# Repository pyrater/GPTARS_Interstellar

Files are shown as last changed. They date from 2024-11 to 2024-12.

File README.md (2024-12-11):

My Modifications and documentation of the build.
All files printed on Bambu Labs P1S
All "Flexor" parts to be printed in TPU, all others PETG

TPU: https://us.store.bambulab.com/products/tpu-for-ams

PETG: https://us.store.bambulab.com/products/petg-hf

The Default v9 chasis bottom does not allow for installation of a SD card, too close to the wall. Modified that part... will test.  (Chassis Bottom (Mod SD CARD).stl)

Plan:
LLM = ooba/openai/tabby (recommend https://github.com/theroyallab/tabbyAPI)
TTS = local or xttsv2 using xtts-api-server WITH VOICE clone (https://github.com/daswer123/xtts-api-server)
STT = uses vosk
SD = Automatic1111
Vision = Image Classifier

Good Info: https://www.instagram.com/wizard.py/

wizard uses the MG996R 55g Digital RC Servo Motors High Torque Metal Gear Servo
Andrew uses: diymore 6PCS Metal Gear High Speed Torque Digital Servo Moto

-Link: https://www.amazon.com/diymore-6-Pack-MG996R-Digital-Helicopter/dp/B0CGRP59HJ/ref=sr_1_5?sr=8-5

Printing Draft / test is complete:
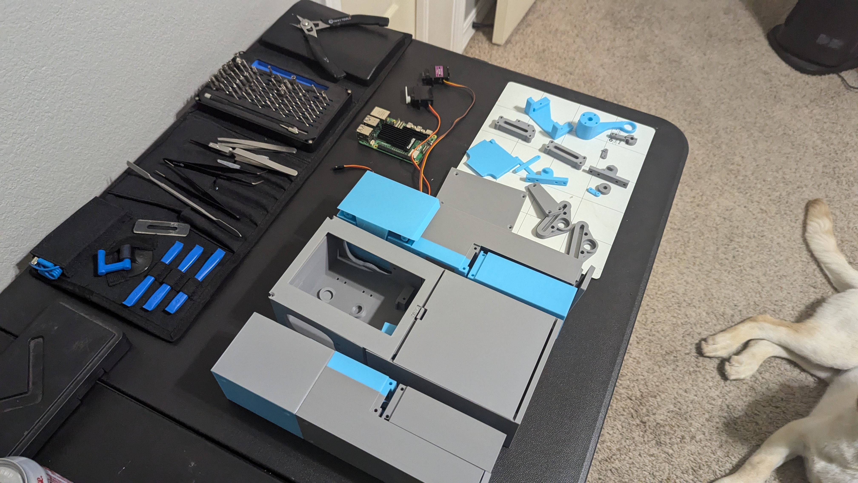
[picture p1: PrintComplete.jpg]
print


Software Demo (all locally hosted RTX 3060 streaming to RPI):
Video Title (https://www.youtube.com/watch?v=4YObs8BV3Mc)

My Hardware:

Screws Needed (atleast):

6  M3 20mm

40 M3 14mm

76 M3 10mm

Rods:
https://www.amazon.com/gp/product/B01MAYQ12S/ref=ox_sc_act_title_1?smid=ATVPDKIKX0DER&psc=1
https://www.amazon.com/gp/product/B0CTSX8SJS/ref=ox_sc_act_title_2?smid=A1NR50YASSZD11

Servos:
https://www.amazon.com/gp/product/B0CGRP59HJ/ref=ox_sc_act_title_3?smid=A3F3CVCOVVNP2J

NOTE: Each leg APPEARS to need 2 90g micro servos if you want exendable arms.

Bolts:
https://www.amazon.com/gp/product/B0CR6DY4SS/ref=ox_sc_act_title_4?smid=A1ZRRCZIF57JQ9
https://www.amazon.com/gp/product/B0D9GW9K4G/ref=ox_sc_act_title_5?smid=A1ZRRCZIF57JQ9
https://www.amazon.com/gp/product/B0CR6G5XWC/ref=ox_sc_act_title_6?smid=A1ZRRCZIF57JQ9
https://www.amazon.com/gp/product/B0CR6F3N45/ref=ox_sc_act_title_7?smid=A1ZRRCZIF57JQ9

Springs:
https://www.amazon.com/gp/product/B076M6SFFP/ref=ox_sc_act_title_8?smid=A1THAZDOWP300U&psc=1

Bearings:
https://www.amazon.com/gp/product/B07FW26HD4/ref=ox_sc_act_title_9?smid=ATVPDKIKX0DER&psc=1

16-Channel 12-bit PWM Servo Driver with I2C Interface:
https://www.amazon.com/gp/product/B00EIB0U7A/ref=ox_sc_act_title_10?smid=AAEX2EKCSXB7D&psc=1

RPI Mic:
https://www.amazon.com/gp/product/B086DRRP79/ref=ox_sc_act_title_11?smid=A1DWLG2LHSJB8R

Linkage:
https://www.amazon.com/gp/product/B0CRDRWYXW/ref=ox_sc_act_title_12?smid=A1NR50YASSZD11&psc=1

Buck Convertor:
https://www.amazon.com/gp/product/B07SGJSLDL/ref=ox_sc_act_title_13?smid=A3CX4TQNUXMB0L

RPI 5:
https://www.amazon.com/Raspberry-Pi-Quad-core-Cortex-A76-Processor/dp/B0CTQ3BQLS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

3" LCD:
https://www.amazon.com/OSOYOO-3-5inch-Display-Protective-Raspberry/dp/B09CD9W6NQ/ref=sr_1_8?sr=8-8

Servo Wires:
https://www.amazon.com/OliYin-7-87in-Quadcopter-Extension-Futaba/dp/B0711TBZY2/ref=sr_1_7?sr=8-7

MISC:

Audio amp:
https://www.amazon.com/dp/B0BTBS5NW2

Audio Speaker:
https://www.amazon.com/dp/B07GJ4GH67

Camera:
https://www.amazon.com/dp/B07GJ4GH67

Orginal Fork info:

# TARS from Interstellar x ChatGPT

- Original article: https://www.hackster.io/charlesdiaz/how-to-build-your-own-replica-of-tars-from-interstellar-224833#comments

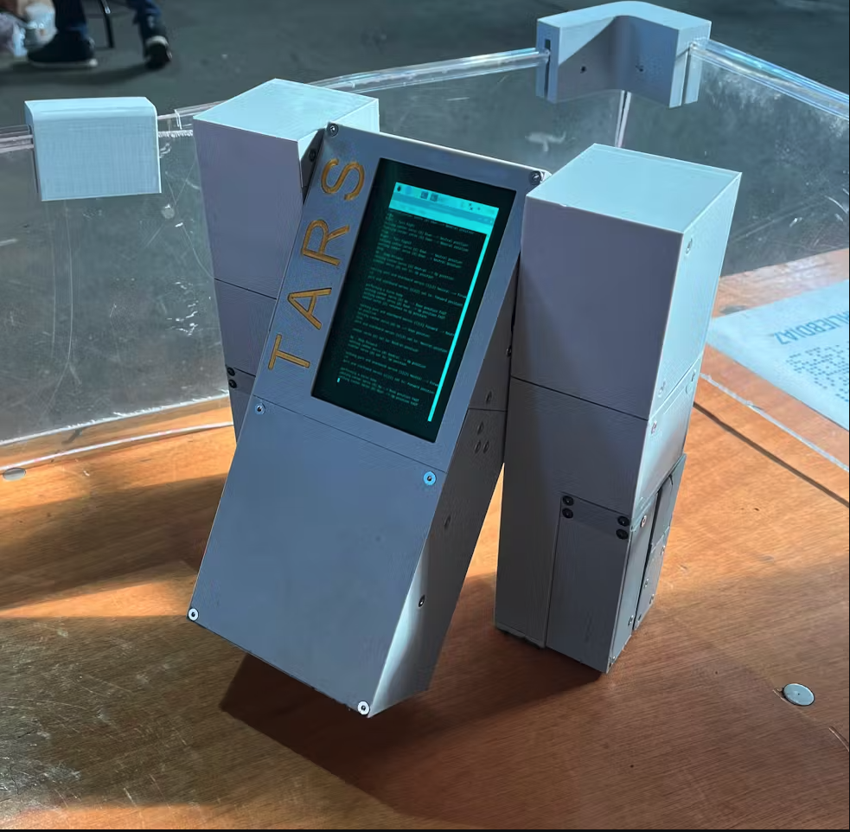
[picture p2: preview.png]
preview


## Files TARS v3_10 - Fix Case Clip

- DOWNLOAD: https://uploadnow.io/f/MPLCGwg | https://fastupload.io/9f3621ef4afe07cc

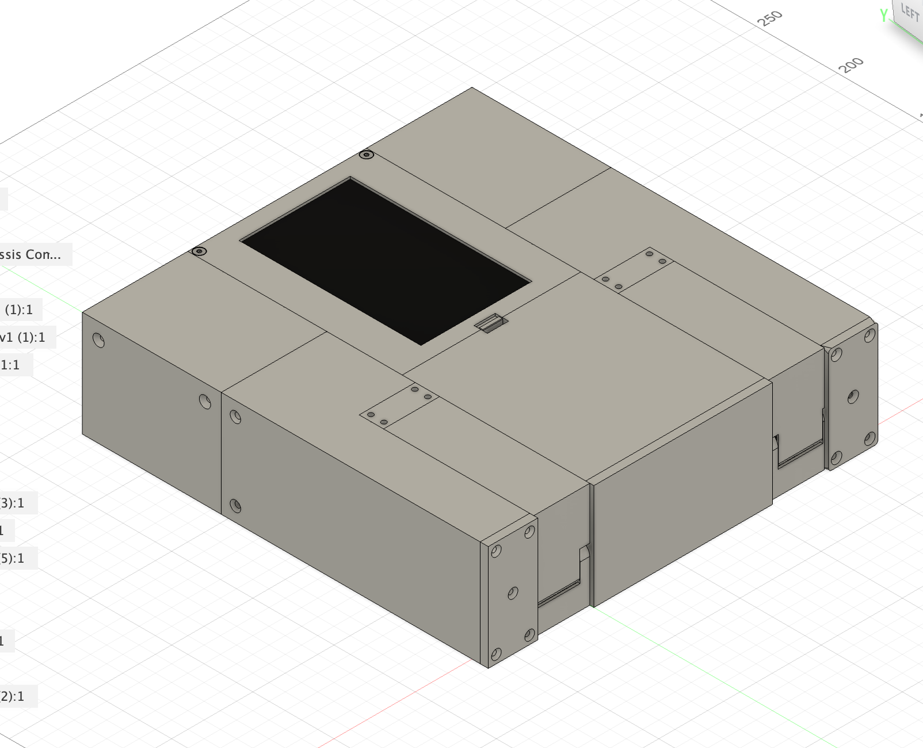
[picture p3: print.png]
print


## Software

- Fusion 360 at https://www.autodesk.com/ca-en/products/fusion-360/personal
- https://projects.raspberrypi.org/en/projects/getting-started-with-the-pico/2
- OS Pi: https://www.raspberrypi.com/software/

## Tutorial

- OS SD Card: https://www.tomshardware.com/how-to/set-up-raspberry-pi

### Adafruit 16-Channel PWM HAT with a Raspberry Pi

- Videos https://www.youtube.com/watch?v=bB-xymRI8BY,
- Documentation: https://learn.adafruit.com/adafruit-16-channel-pwm-servo-hat-for-raspberry-pi, https://core-electronics.com.au/guides/raspberry-pi/servo-hat-raspberry-pi/

### Without HAT

- Videos: https://www.youtube.com/watch?v=ea6tSppgZlY, https://www.youtube.com/watch?v=9jcEwn7GzNs, https://www.youtube.com/watch?v=40tZQPd3z8g
- Documentation: https://learn.adafruit.com/adafruits-raspberry-pi-lesson-8-using-a-servo-motor/overview, https://learn.adafruit.com/adafruit-16-channel-servo-driver-with-raspberry-pi/configuring-your-pi-for-i2c, https://www.youtube.com/watch?v=-x2EEIUMm6A

## 3D Printing

- Steel / Stainless / Aluminium: https://forgelabs.ca/
- PLA / ABS: https://jlc3dp.com/3d-printing-quote or https://www.treatstock.com/

## Hardware

#### Power

- 1 x 12V to 6V 3A DC at https://www.aliexpress.com/item/32968137531.html
- https://www.aliexpress.com/item/1005003160082010.html
- 1 x 5V DC 4A Fixed 2.1mm Tip Appliance Plugpack at https://www.amazon.ca/Power-Adapter-100-240V-Transformers-Supply/dp/B087LY41PV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
- 1 x 5V 4A DC Power Adapter at https://www.aliexpress.com/item/1005004589869667.html (Used for testing before buying battery)
- 1 x 5V USB To DC DC Power Cable 5.5\*2.1m at https://www.aliexpress.com/item/1005007296667037.html
- 200000mAh Portable Solar Power Bank External Battery Fast Charging Waterproof Powerbank with SOS Flashlight Poverbank for Xiaomi at https://www.aliexpress.com/item/1005006959367711.html, https://www.aliexpress.com/item/1005007306992861.html

Please use HDMI cable: fpv cable hdmi, HDMI-compatible,FPV HDMI ffc HDMI Ribbon Cable 90 Degree Mini/Micro HDMI to Standard HDMI PCB Connector 20pin fpv micro hdmi 15cm

---

#### Hardware

- 1 x https://www.aliexpress.com/item/32914198349.html

- 2 x Lightweight Actobotics Servo Horn (H25T Spline) at https://www.servocity.com/25t-lightweight-hub-horn/ or look at .step file
- 1 x Adafruit 16-Channel 12-bit PWM/Servo Driver at https://www.adafruit.com/product/2327
- 1 x 8Bitdo Zero 2 Bluetooth at https://www.aliexpress.com/item/1005006458561670.html
-
- 5 x LD-3015MG 17KG 270 (LewanSoul LD-3015MG Standard Full Metal Gear Digital Servo with 17kg High Torque Dual Ball Bearing for RC Robot Car) at https://www.aliexpress.com/item/32787763122.html (2000-0025-0002)
- 1 x Fataba s3003 90-180deg at https://www.aliexpress.com/item/32957714272.html
- 4 x 2903-0004-0245 assembly at https://www.gobilda.com/2903-series-nylon-ball-linkage-m4-24-5mm-length-4-pack / Linkeage Rod M4 at https://www.aliexpress.com/item/1005005616106307.html
- 10 x Flexor bolts at https://www.aliexpress.com/item/32969042589.html

- 10 x Hex M3 20mm, 10 x Hex M3 10mm, 10 x Hex M3 14mm, 10 x Hex M3 30mm at https://www.aliexpress.com/item/1005003184392748.html
- 1 x Bearing 6x15x5 https://www.aliexpress.com/item/4000909583668.html
- 1 x Compression Spring 0.5mmx20mmx11mm https://www.aliexpress.com/item/1005005312536098.html

---

#### CPU & Storage

- 1 x MicroSD Card at https://www.aliexpress.com/item/1005006693506827.html
- 1 x Raspberri 3B/3B+ at https://www.adafruit.com/raspberrypi3bplus or eBay
- 1 x Elecrow 5 inch Touchscreen Portable Monitor HDMI-compatible 800x480 at https://www.aliexpress.com/item/32889893278.html

---

#### Battery

- 1 x myCharge Hub Mini at https://www.target.com/p/mycharge-hub-mini-3350mah-2-4a-output-power-bank-with-integrated-charging-cables-silver/-/A-76625534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
- 1 x Zeee 11.1V 120C 1500mAh 3S at https://www.amazon.ca/Zeee-Graphene-Quadcopter-Airplane-Helicopter/dp/B08P399N54/

## Extra

- Face Recognition: https://core-electronics.com.au/guides/face-identify-raspberry-pi/
- Lidar Detection: MS200 Lidar Sensor Kit Portable 360°TOF Ranging Scanner 12m Range Support ROS1 and ROS2 For ROS Robot Raspberry Pi Jetson NANO
- Battery Level: https://learn.sparkfun.com/tutorials/ltc4150-coulomb-counter-hookup-guide, https://forums.raspberrypi.com/viewtopic.php?t=173046, https://forums.raspberrypi.com/viewtopic.php?t=340930

## ChatGPT

- https://www.youtube.com/watch?v=N0718RfpuWE

## Servo Abstractor - Python

> Sort of redundant to give these functions their own file, but this program takes the basic servo movements from the servo controller file and combines them to automate walking functions.

## TARS Runner - Python

> Run this file in terminal on your onboard computer to initialize TARS. This file handles communication with the bluetooth remote.

## Servo Controller - Python

> Handles basic movements of servos in TARS. Communicates with an Adafruit PCA9685 servo driver to control the servos.

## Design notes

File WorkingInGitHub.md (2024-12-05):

# Contributing to GPTARS_Interstellar

Welcome to the GPTARS_Interstellar community! We're excited to have you contribute code, CAD files, documentation, or related content to this project. This guide is for folks new to GitHub to help you quickly get setup to collaborate on the project.

> "Everybody good? Plenty of slaves for my robot colony?" -TARS

---

## **What You Can Contribute**
This project includes:
- **Binary CAD files** (e.g., STEP, STL)
- **Code**
- **Documentation**
- **Related content**

The primary repository is maintained by pyrater: [GPTARS_Interstellar on GitHub](https://github.com/pyrater/GPTARS_Interstellar).
Join us in discord https://discord.gg/UfQpGXPW #repo for related questions and discussions.
---

## **For Experienced GitHub Users**
- Fork the repo and submit pull requests (PRs) to [pyrater/GPTARS_Interstellar](https://github.com/pyrater/GPTARS_Interstellar).
- Notify pyrater on Discord in the `#repo` channel if your PR is ready for review.

---

## **For New Git and GitHub Users**

Never used Git or GitHub before? No problem! This section will guide you through the basic steps to get started.

### **Step 1: Create a GitHub Account**
- Sign up for a free GitHub account: [Create an account](https://docs.github.com/en/get-started/start-your-journey/creating-an-account-on-github).

### **Step 2: Fork the Repository**
1. Go to [GPTARS_Interstellar on GitHub](https://github.com/pyrater/GPTARS_Interstellar).
2. Click the **Fork** button in the top-right corner.
3. Select **Create a new fork** to make your own copy of the repository. This fork will look like `yourGithubUsername/GPTARS_Interstellar`.

Why fork? Forking allows you to make changes in your own copy of the repository without affecting the original.

### **Step 3: Install Git Locally**
If you’re new to Git, you’ll need to install it on your local machine.
- Download Git: [Git Downloads](https://git-scm.com/downloads).
- Verify the installation by running `git --version` in your command line.

### **Step 4: Secure Your GitHub Account**
- Protect your account with multi-factor authentication (MFA): [Set up MFA](https://docs.github.com/en/authentication/keeping-your-account-and-data-secure/about-authentication-to-github).
- **Highly Recommended**: Set up an SSH key for secure and streamlined operations: [Generate an SSH Key](https://docs.github.com/en/authentication/connecting-to-github-with-ssh/generating-a-new-ssh-key-and-adding-it-to-the-ssh-agent).

### **Step 5: Clone Your Fork**
1. Open a terminal or command prompt.
2. Navigate to the folder where you want to store the repository.
3. Clone your fork:
   ```bash
   git clone git@github.com:yourGithubUsername/GPTARS_Interstellar.git
   ```
4. Navigate into the project folder:
   ```bash
   cd GPTARS_Interstellar
   ```

### **Step 6: Set Up Remotes**
- Check the remote URLs:
  ```bash
  git remote -v
  ```
  You should see your fork as `origin`.
- Add pyrater's repository as the upstream remote:
  ```bash
  git remote add upstream git@github.com:pyrater/GPTARS_Interstellar.git
  ```

Why? This setup helps you fetch updates from the main repository to keep your fork up-to-date.

---

## **Basic Git Operations**
These are the standard steps for making contributions:

### **1. Create a Branch**
Always create a new branch for your work:
```bash
git checkout -b your-branch-name
```

Branches help you isolate changes and organize features.

### **2. Make Changes**
- Add, edit, or delete files in the project.
- Use descriptive branch names, e.g., `add-new-feature` or `fix-bug`.

### **3. Stage Changes**
Stage your changes to prepare them for a commit:
```bash
git add .
```
Optionally, check the status:
```bash
git status
```

### **4. Commit Changes**
Save your changes locally with a meaningful commit message:
```bash
git commit -m "Your commit message here"
```

For non-binary files, Git tracks changes for version control. For CAD files like STL or STEP, Git stores the files as blobs without versioning.

### **5. Push Changes**
Push your branch to your fork on GitHub:
```bash
git push origin your-branch-name
```

---

## **Creating a Pull Request (PR)**
Once your changes are ready:
1. Go to pyrater's repository: [GPTARS_Interstellar](https://github.com/pyrater/GPTARS_Interstellar).
2. Click **Pull requests** in the top menu.
3. Click the green **New pull request** button.

On the **Comparing changes** page:
- **Base repository**: `pyrater/GPTARS_Interstellar`, base: `main`.
- **Head repository**: `yourGithubUsername/GPTARS_Interstellar`, compare: `your-branch-name`.

### **Provide Details**
- Add a meaningful title for your PR.
- Write a clear description of your changes, explaining what they do and why they’re needed.
- Confirm the changed files are correct.

### **Submit the PR**
- Click **Create pull request**.
- Notify pyrater on Discord in the `#repo` channel.

### **Review and Approval**
- Wait for pyrater to review your PR.
- If changes are requested, update your branch locally, commit, and push again. GitHub will automatically update the PR.
- Once approved, your changes will be merged into the main repository. Congratulations!

---

## **Keeping Your Fork Up-to-Date**
If other contributors make changes to the main repository, keep your fork in sync:
1. Fetch updates from the upstream repository:
   ```bash
   git fetch upstream
   ```
2. Merge updates into your branch:
   ```bash
   git merge upstream/main
   ```
3. Push updates to your fork:
   ```bash
   git push origin your-branch-name
   ```

---

## **Additional Resources**
- [Git Basics](https://git-scm.com/doc)
- [GitHub Docs](https://docs.github.com)
- [Common Git Commands Cheat Sheet](https://education.github.com/git-cheat-sheet-education.pdf)
- [Visual Studio Code - Working with GitHub](https://code.visualstudio.com/docs/sourcecontrol/github)

---

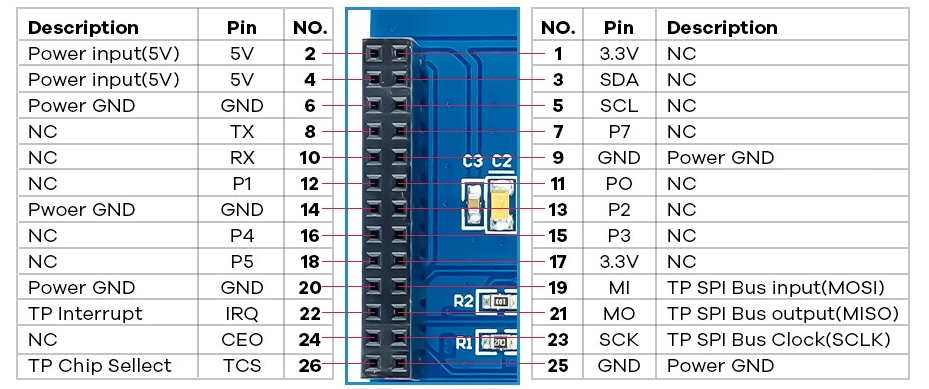
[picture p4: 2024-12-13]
Hardware/Screenshot 2024-12-10 121338.png

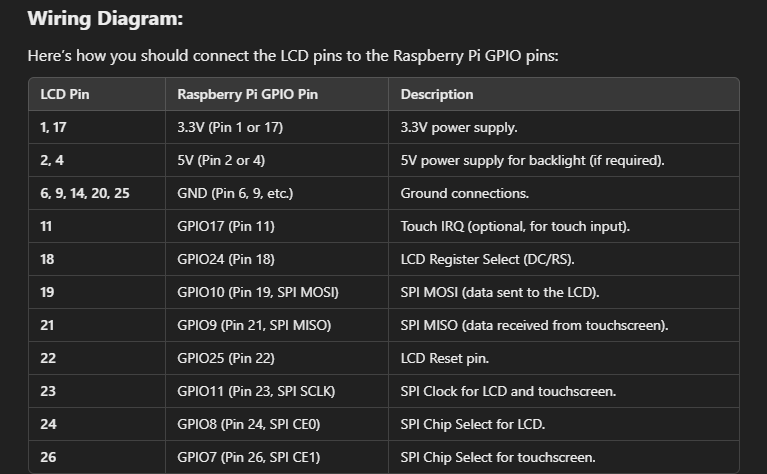
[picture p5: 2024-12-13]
Hardware/Screenshot 2024-12-10 131234.png

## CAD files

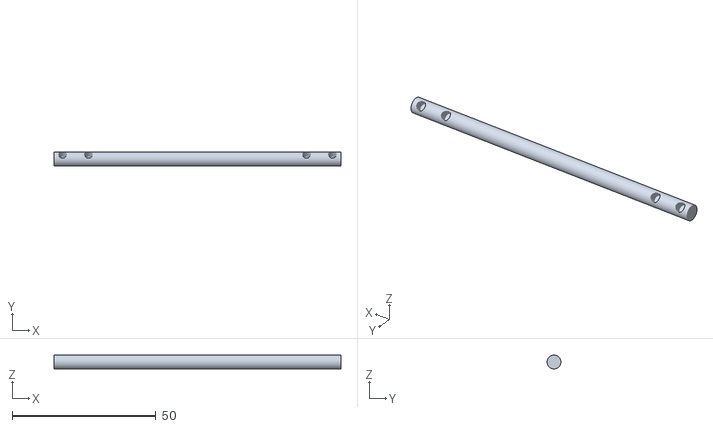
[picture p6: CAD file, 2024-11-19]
3d Printer Files/Main Axle.stl
100.0 x 4.80 x 4.80

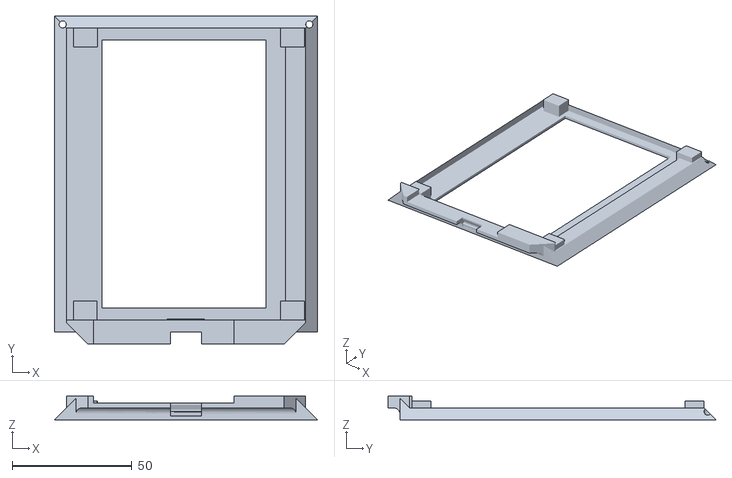
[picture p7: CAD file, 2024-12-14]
3d Printer Files/Chassis Upper Lid MOD 5inch HDMI screen (v10).stl
110.0 x 137.0 x 10.0

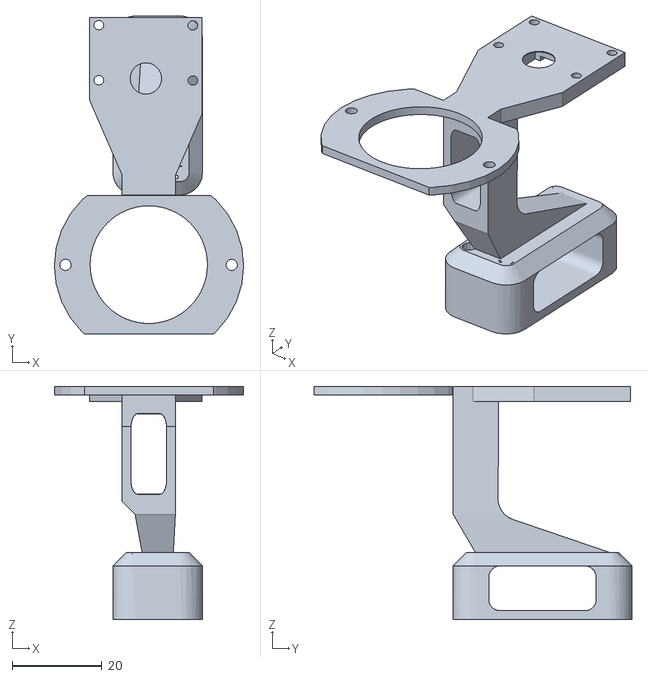
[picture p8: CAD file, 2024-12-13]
3d Printer Files/Other/RPI CAM and Speaker Mount.stl
42.3 x 71.1 x 52.1

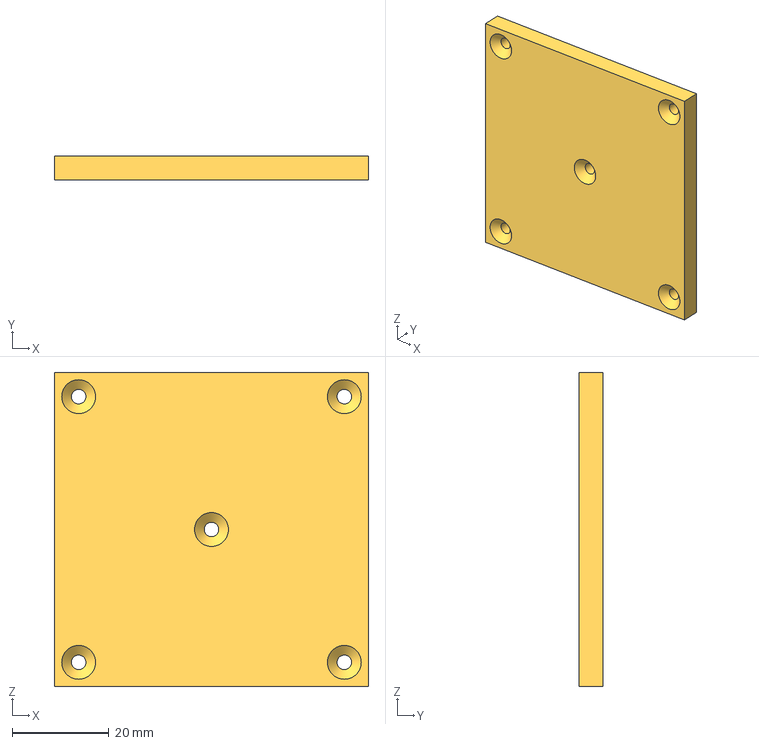
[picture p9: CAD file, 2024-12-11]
3d Printer Files/simplified_tars/footpad-simplified.3mf
65.0 x 5.00 x 65.0 mm

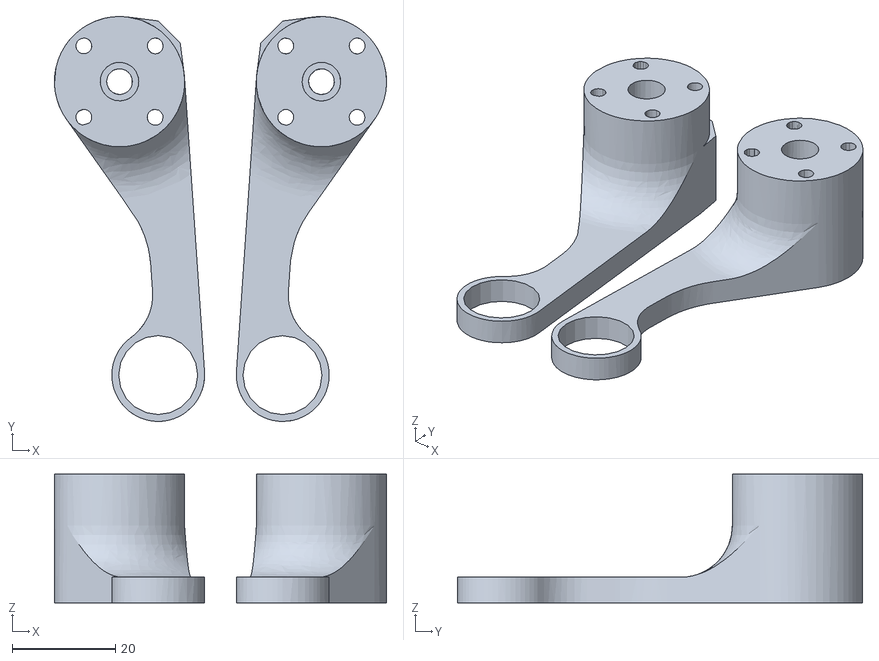
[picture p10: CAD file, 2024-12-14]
3d Printer Files/Arm Right&Left Mount Bigger bearinghole.stl
64.4 x 78.5 x 25.0

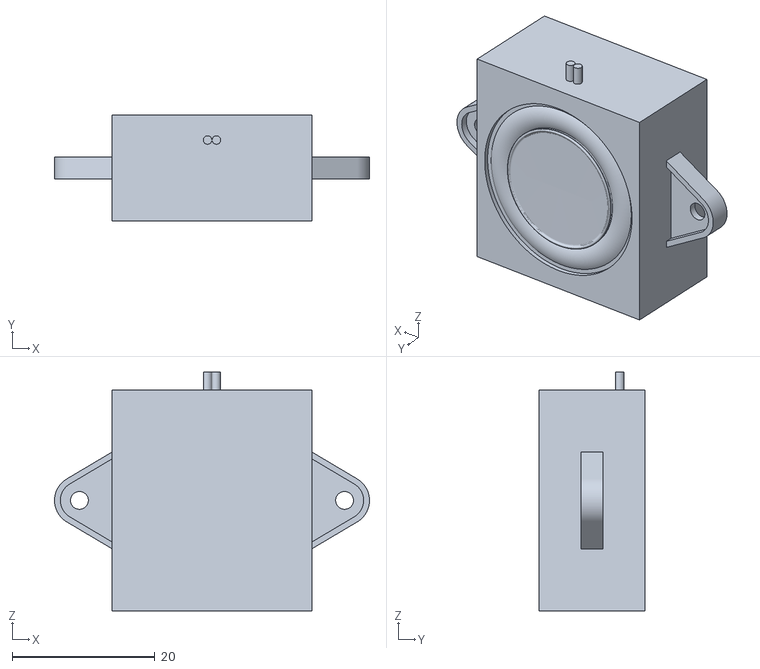
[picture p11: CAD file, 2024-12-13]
3d Printer Files/Other/Speaker.stl
44.2 x 14.9 x 33.5

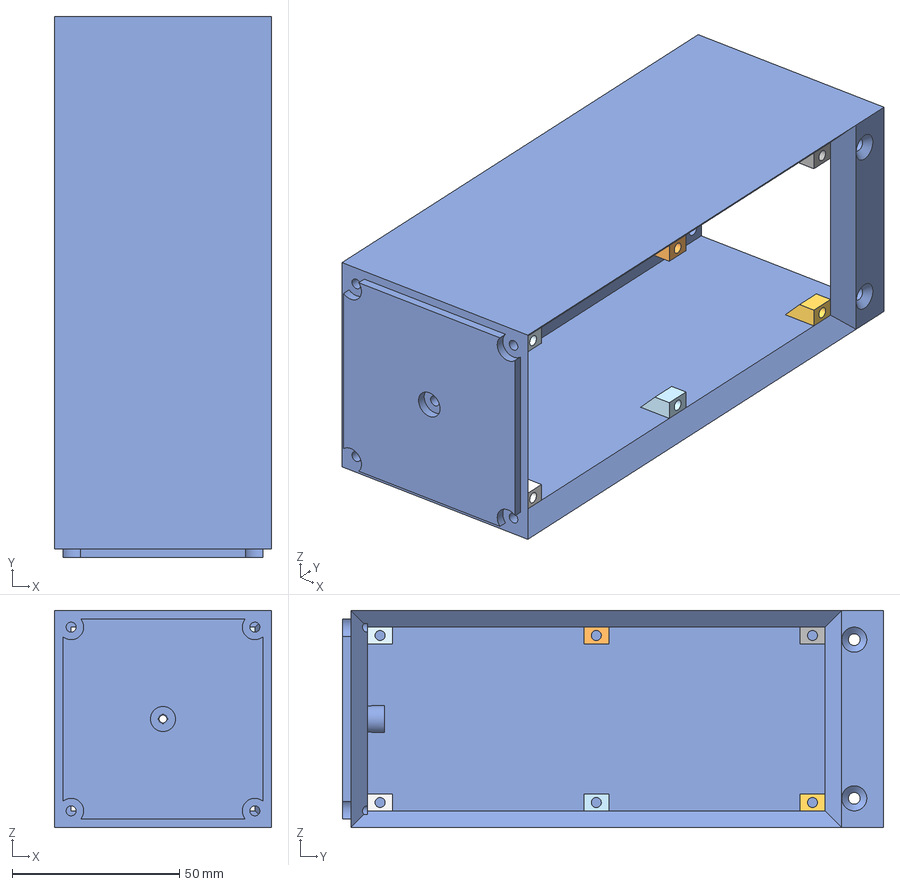
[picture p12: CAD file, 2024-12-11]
3d Printer Files/simplified_tars/leg - simplified.3mf
65.0 x 162.0 x 65.0 mm

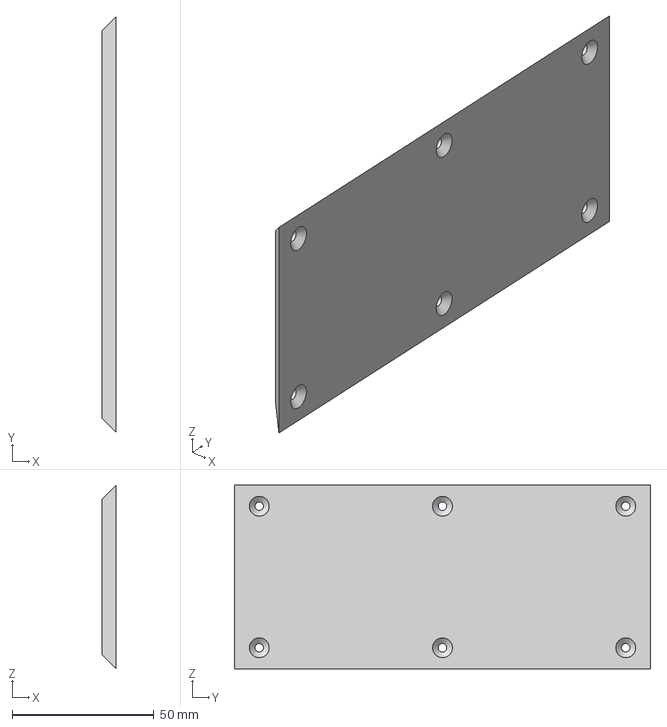
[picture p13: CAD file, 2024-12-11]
3d Printer Files/simplified_tars/leg_simplified-lid.3mf
5.00 x 147.0 x 65.0 mm

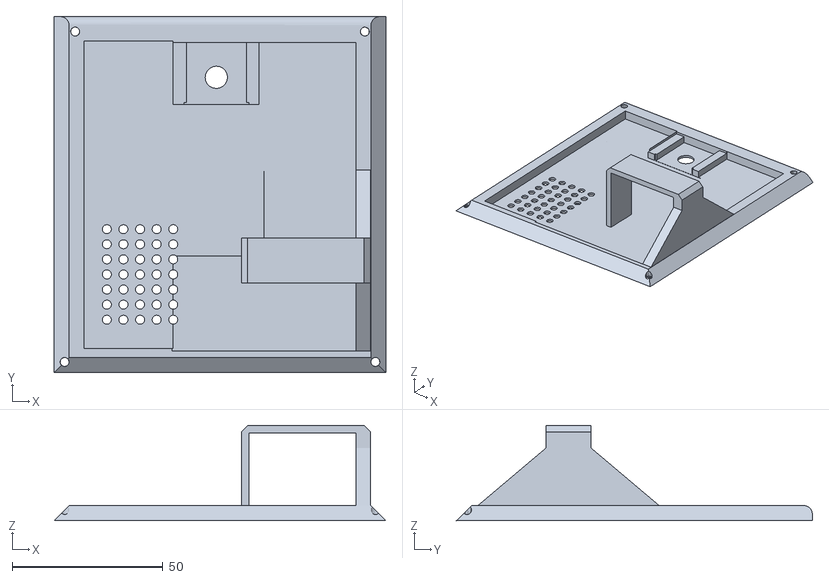
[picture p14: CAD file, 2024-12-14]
3d Printer Files/Chassis Lower Lid MOD LiPo flat-camerahole-speakerholes (v9).stl
110.0 x 118.0 x 31.5

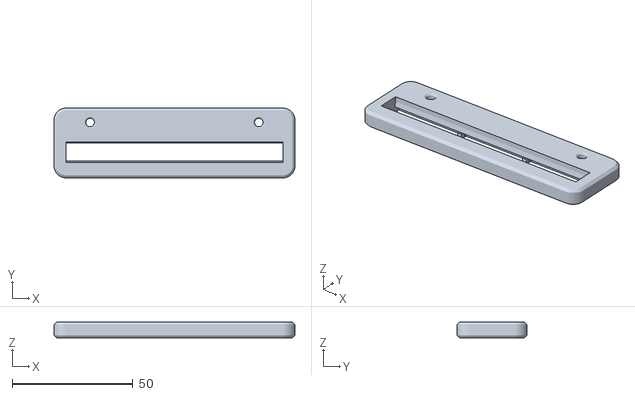
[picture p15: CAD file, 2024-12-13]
3d Printer Files/Other/PCT Linear Base Mount.stl
100.0 x 29.0 x 6.50

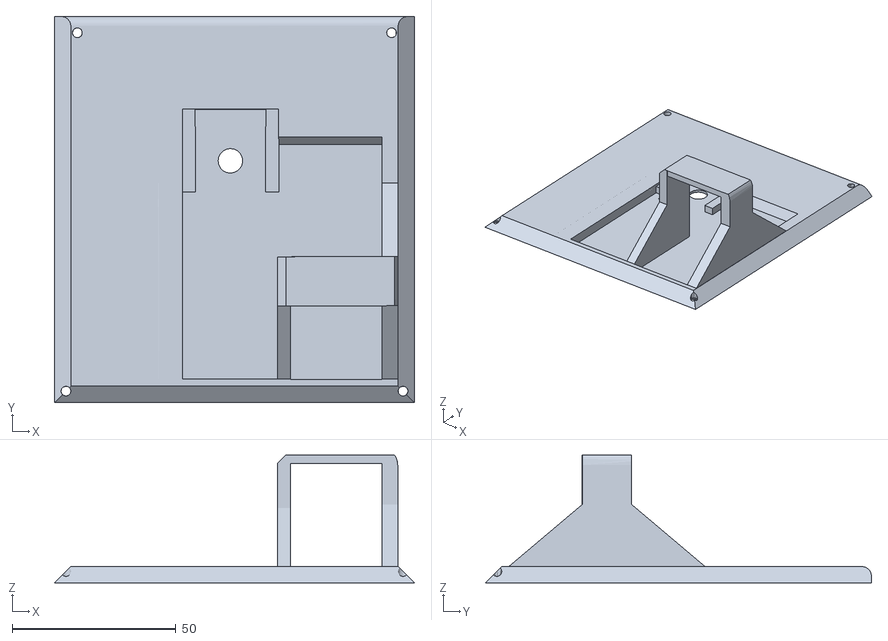
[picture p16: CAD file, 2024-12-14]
3d Printer Files/Chassis Lower Lid MOD LiPo and camerahole- (v9).stl
110.0 x 118.0 x 39.1

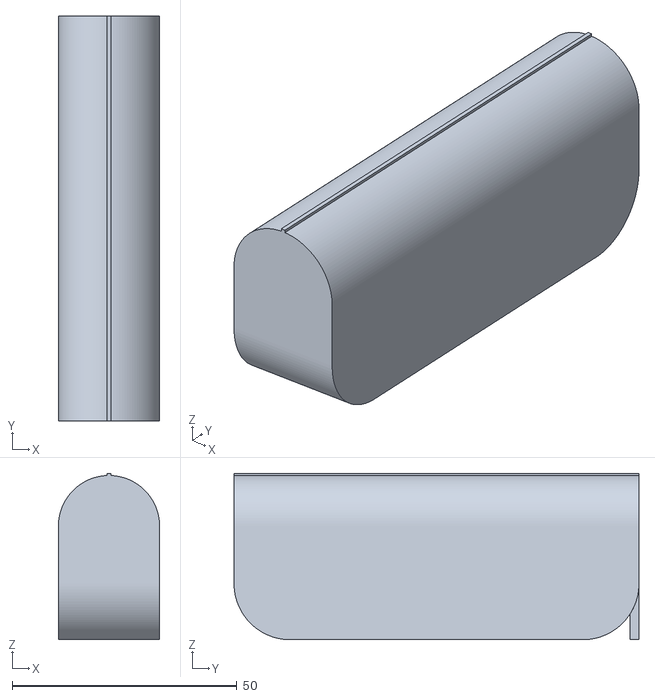
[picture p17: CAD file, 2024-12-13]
3d Printer Files/Other/battery.stl
22.5 x 90.0 x 37.0

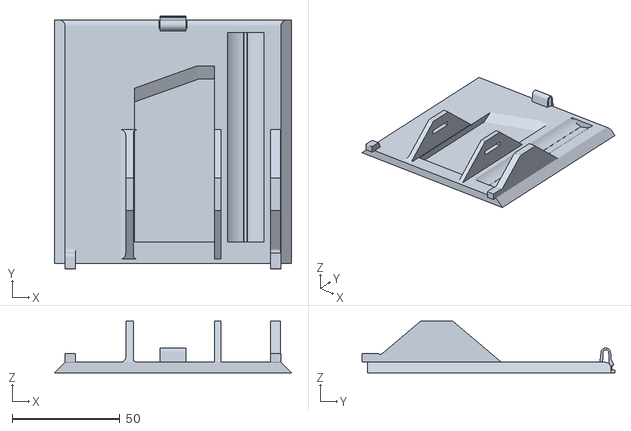
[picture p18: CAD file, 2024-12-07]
3d Printer Files/Chassis Lower Lid MOD slotted open batt bracket (v10).stl
110.0 x 117.3 x 24.1

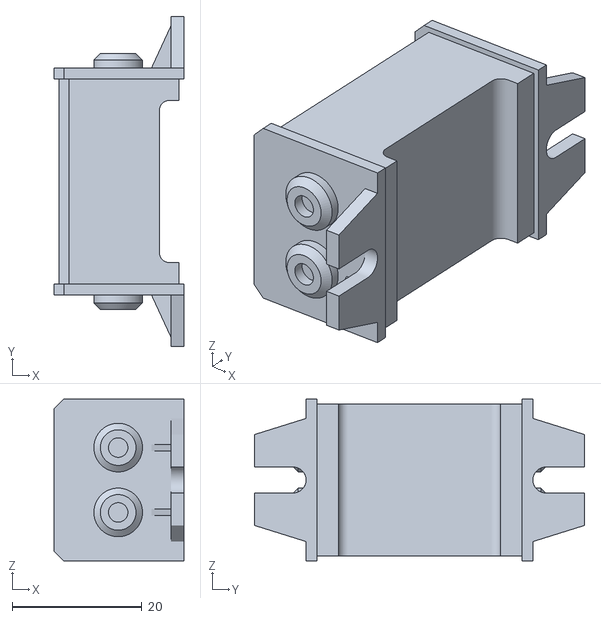
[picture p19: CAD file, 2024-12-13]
3d Printer Files/Other/buck convertor.stl
20.0 x 51.0 x 25.0

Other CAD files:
3d Printer Files/Chassis Lower Lid MOD open batt clip (v9).stl
3d Printer Files/Other/lipo.stl
3d Printer Files/Chassis Lower (v10) SDCARD MOD.stl
3d Printer Files/Other/12 ch pwm.stl
3d Printer Files/Arm Chasis Lid x2.stl
3d Printer Files/Arm Left (Top Chassis).stl
3d Printer Files/Arm Left 1 Finger.stl
3d Printer Files/Arm Left 2 Finger.stl
3d Printer Files/Arm Left Footpad.stl
3d Printer Files/Arm Left Insert.stl
3d Printer Files/Arm Left Long Finger Lid.stl
3d Printer Files/Arm Left Long Finger.stl
3d Printer Files/Arm Left Lower Chasis.stl
3d Printer Files/Arm Left Lower Chassis MOD 3mm servoscrews.stl
3d Printer Files/Arm Left Mount.stl
3d Printer Files/Arm Left NP - Mount Bearing.stl
3d Printer Files/Arm Left Small Finger Lid.stl
3d Printer Files/Arm Left Spring Driver.stl
3d Printer Files/Arm Left Top Lid.stl
3d Printer Files/Arm Right (Top Chassis).stl
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

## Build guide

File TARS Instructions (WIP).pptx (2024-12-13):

## TARS Instructions

Screws Needed:
6 M20
40 M14
76 M10

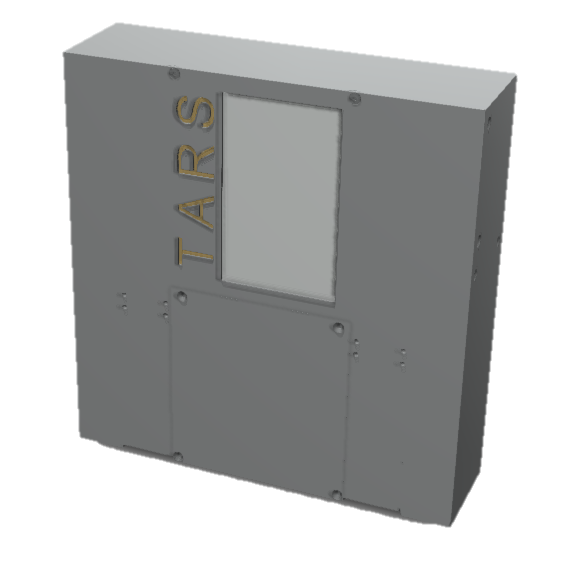
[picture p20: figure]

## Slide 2

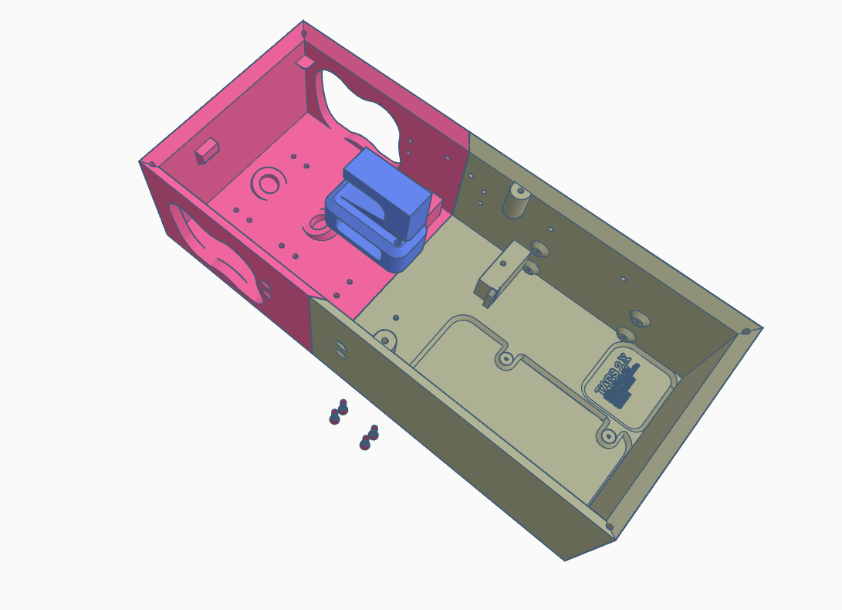
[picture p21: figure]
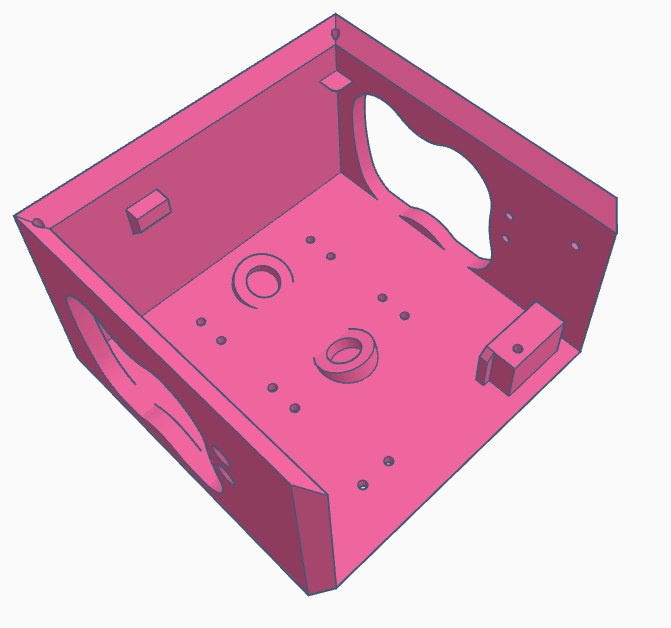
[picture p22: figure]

Chassis Upper (v9)

Chassis Lower (v9)

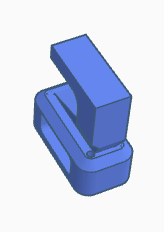
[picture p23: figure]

Chassis Connector Screen Support

M3 20MM x4

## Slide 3

x2

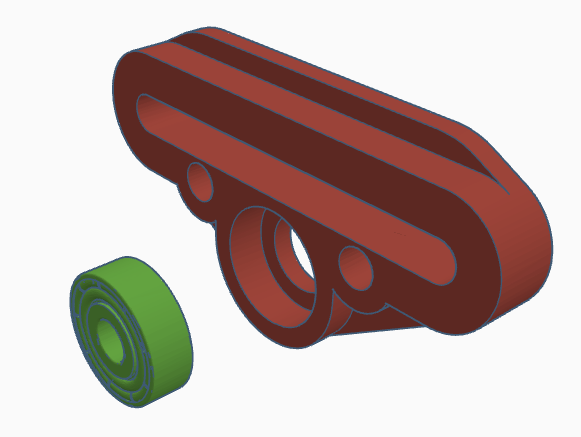
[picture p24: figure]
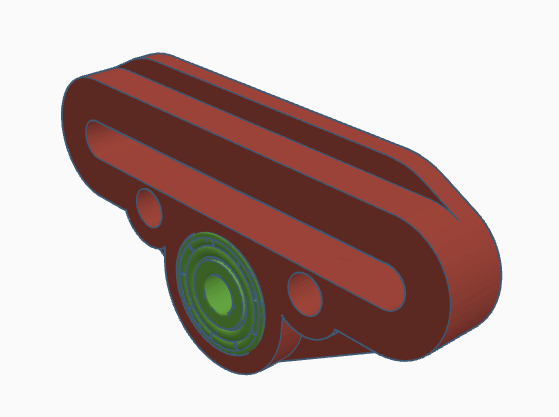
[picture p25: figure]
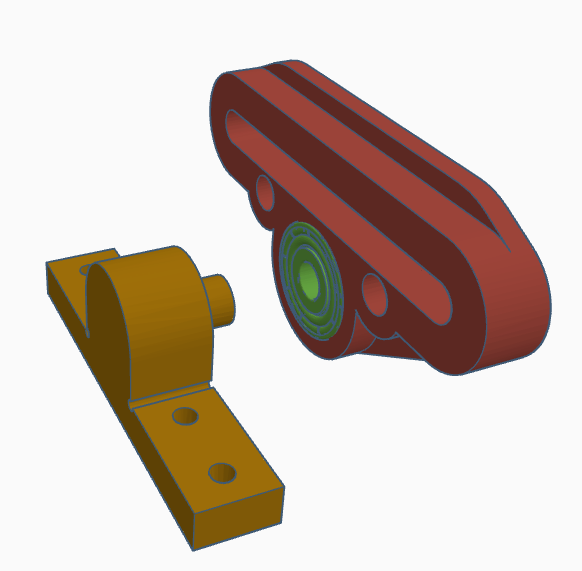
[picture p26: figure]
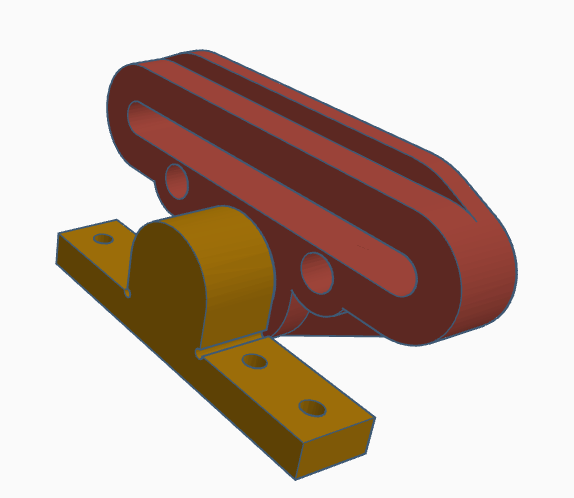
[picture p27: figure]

Arm Spring Divider
(left and Right)

608 Bearing
(metal or Printed)

Arm Suspension Mount

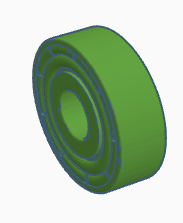
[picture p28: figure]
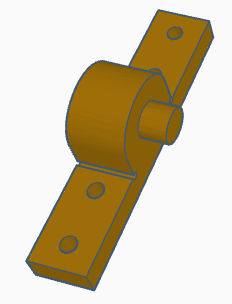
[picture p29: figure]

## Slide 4

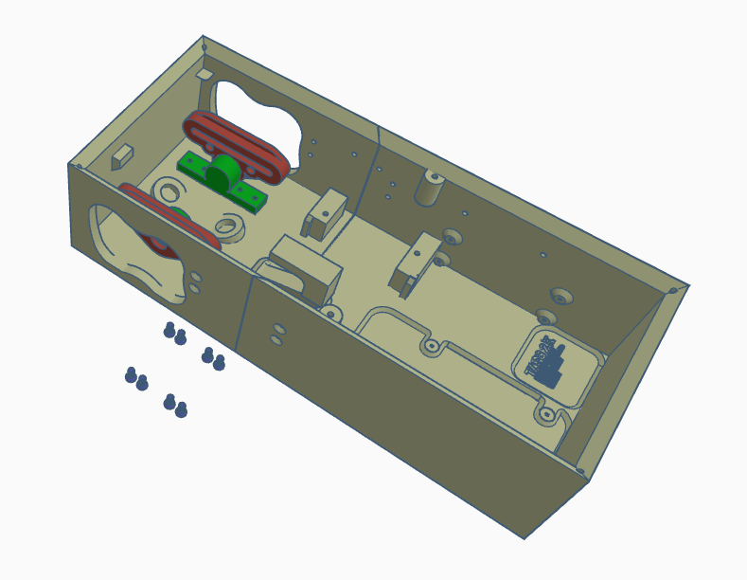
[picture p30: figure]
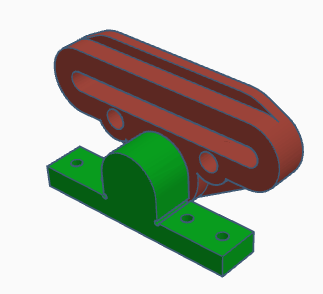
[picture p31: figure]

Assembly from previous step x2

Arm Suspension Mount x8

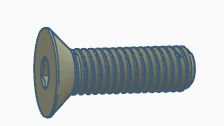
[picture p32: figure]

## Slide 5

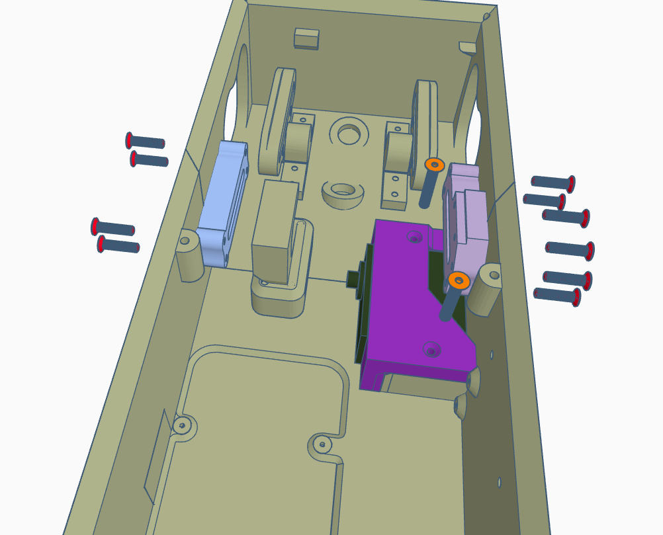
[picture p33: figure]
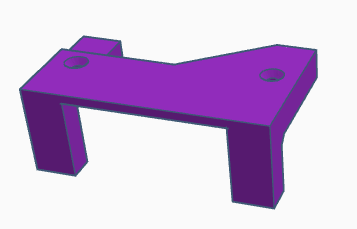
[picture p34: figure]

Chassis Lower Servo Mount

Servo

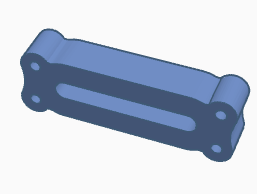
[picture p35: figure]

Sus Mount (1)

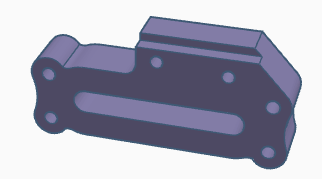
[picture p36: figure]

SUS Mount

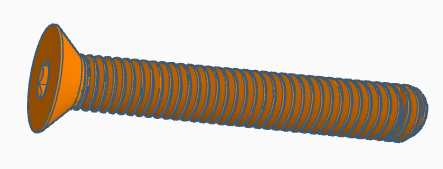
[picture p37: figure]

M3 20MM x2

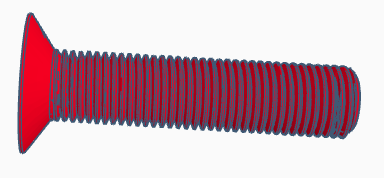
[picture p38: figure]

M3 14MM x10

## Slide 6

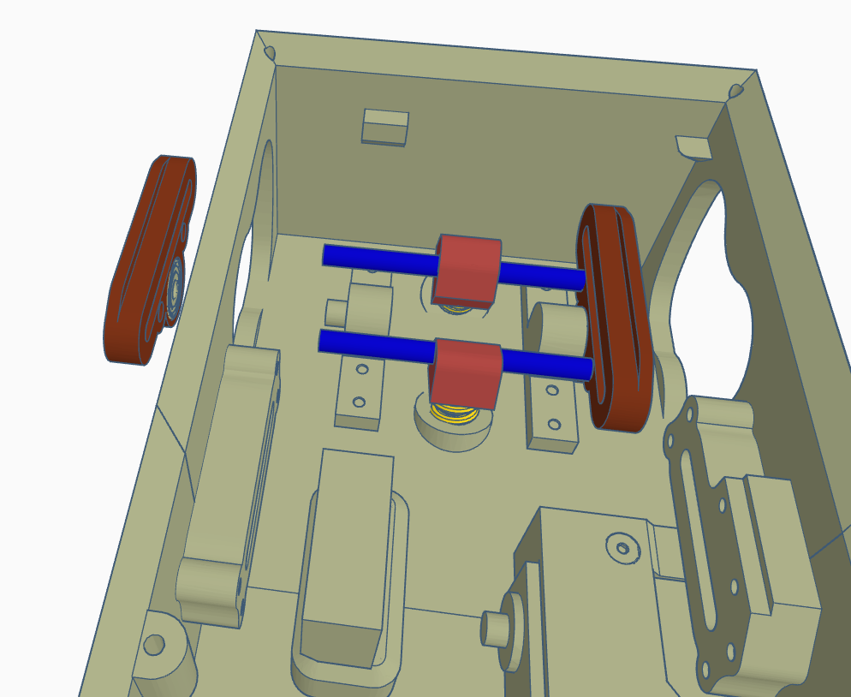
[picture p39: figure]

Secondary Axle x2

Spring x2

Upper Strut Mount x2

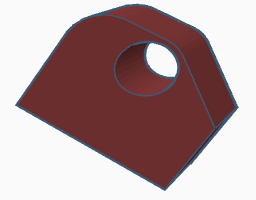
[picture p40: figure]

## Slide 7

x2

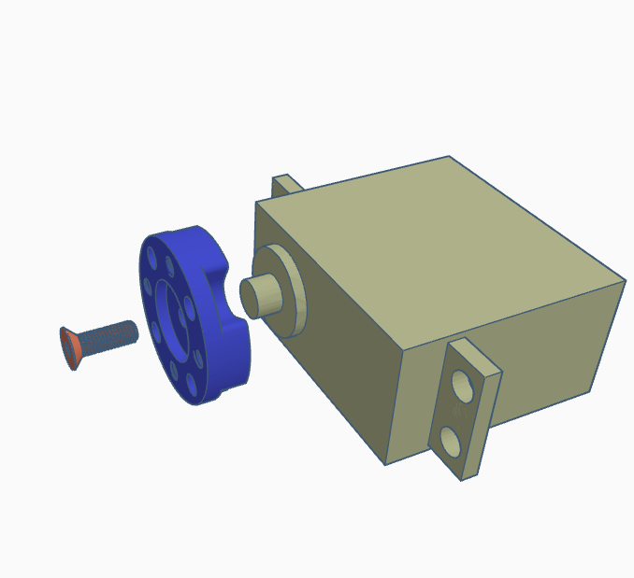
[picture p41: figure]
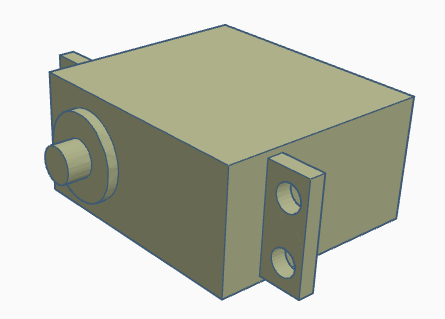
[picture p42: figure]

Servo

Arm Upper Servo Horn

Servo Horn Screw

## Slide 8

x2

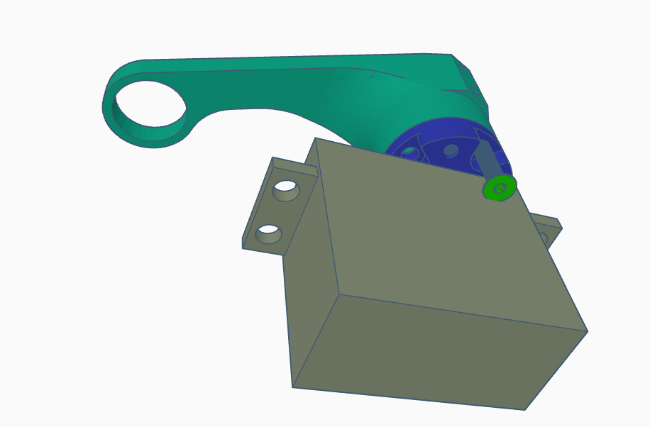
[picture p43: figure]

Servo

Arm Upper Servo Horn

M3 14MM x4

*Rotate the servo to align the bolts

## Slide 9

x2

Servo

Arm Upper Servo Horn

M3 14MM x4

*Rotate the servo to align the bolts

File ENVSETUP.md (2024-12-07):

# ENVSETUP.md

## Hardware Prerequisites

1. **PC with NVIDIA GPU**: Ensure you have a PC with an NVIDIA GPU available for running the XTTS server.

2. **Raspberry Pi**: For obvious reasons.

---

## Step-by-Step Guide (FOR WINDOWS)

### 1. Prepare Your PC with NVIDIA GPU
The TTS server must run on your GPU-enabled PC due to its computational requirements.

1. Ensure **Python 3.9-3.12** is installed on your PC.
2. Install **CUDA** and **cuDNN** compatible with your NVIDIA GPU - [CUDA Installation](https://www.youtube.com/watch?v=krAUwYslS8E)
3. Install **PyTorch** compatible with your CUDA and cuDNN versions - [PyTorch Installation](https://pytorch.org/get-started/locally/)

---

### 2. Set Up XTTS API Server

#### A. Install XTTS API Server
Run the following command on your GPU-enabled PC to clone the [XTTS API Server repository](https://github.com/daswer123/xtts-api-server):

```bash
git clone https://github.com/daswer123/xtts-api-server.git
```

Follow the installation guide for your operating system:
- **Windows**:
  1. Create and activate a virtual environment:
     ```bash
     python -m venv venv
     venv\Scripts\activate
     ```
  2. Install xtts-api-server:
     ```bash
     pip install xtts-api-server
     ```

For more details, refer to the official [XTTS API Server Installation Guide](https://github.com/daswer123/xtts-api-server/tree/main).

#### B. Add the TARS.wav Speaker File
1. Download the `TARS-short.wav` and `TARS-long.wav` files from the `GPTARS_Interstellar` repository under `Brain/TTS/wakewords
/VoiceClones`. These will be the different voices you can use for TARS.
2. Place it in the `speakers/` directory within the XTTS project folder. If the directory does not exist, create it.

#### C. Start the XTTS API Server
1. Open a terminal in the `xtts-api-server` project directory.
2. Activate your virtual environment if not already active:
3. Start the XTTS API Server:
   ```bash
   python -m xtts_api_server --listen --port 8020
   ```
4. Once the server is running, open a browser and navigate to:
   ```
   http://localhost:8020/docs
   ```
5. This will open the API's Swagger documentation interface, which you can use to test the server and its endpoints.

#### D. Verify the Server
1. Locate the **GET /speakers** endpoint in the API documentation.
2. Click **"Try it out"** and then **"Execute"** to test the endpoint.
3. Ensure the response includes the `TARS-Short` and `TARS-Long` speaker files, with entries similar to:
   ```json
   [
     {
       "name": "TARS-Long",
       "voice_id": "TARS-Long",
       "preview_url": "http://localhost:8020/sample/TARS-Long.wav"
     },
     {
       "name": "TARS-Short",
       "voice_id": "TARS-Short",
       "preview_url": "http://localhost:8020/sample/TARS-Short.wav"
     }
   ]
   ```
4. Locate the **POST /tts_to_audio** endpoint in the API documentation.
5. Click **"Try it out"** and input the following JSON in the **Request Body**:
   ```json
   {
       "text": "Hello, this is TARS speaking.",
       "speaker_wav": "TARS-Short",
       "language": "en"
   }
   ```
6. Click **"Execute"** to send the request.
7. Check the response for a generated audio file. You should see a download field where you can download and listen to the audio output.

---

### 3. Set Up the GPTARS_Interstellar Repository on Raspberry Pi

#### A. Clone the Repository
1. Open a terminal on your Raspberry Pi.
2. Clone the **GPTARS_Interstellar** repository:
   ```bash
   git clone https://github.com/pyrater/GPTARS_Interstellar.git
   ```
3. Navigate to the cloned directory:
   ```bash
   cd GPTARS_Interstellar
   ```

#### B. Install Chromium and Chromedriver
Chromium and Chromedriver are required for Selenium-based operations in the project.

1. **Update Your System**:
   ```bash
   sudo apt update
   sudo apt upgrade -y
   ```

2. **Install Chromium**:
   ```bash
   sudo apt install -y chromium-browser
   ```

3. **Install Chromedriver for Selenium**:
   ```bash
   sudo apt install -y chromium-chromedriver
   ```

4. **Verify Installations**:

   - Check Chromium installation:
     ```bash
     chromium-browser --version
     ```
   - Check Chromedriver installation:
     ```bash
     chromedriver --version
     ```

#### C. Set Up the Python Environment

1. Create a virtual environment:
   ```bash
   python3 -m venv venv
   ```
2. Activate the virtual environment:
   ```bash
   source venv/bin/activate
   ```
3. Install the required dependencies under `Brain/`:
   ```bash
   pip install -r requirements.txt
   ```

#### D. Connect Hardware

1. Connect your **microphone** to the Raspberry Pi via USB.
2. Connect your **speaker** to the Raspberry Pi using the audio output or Bluetooth.

#### E. Set the API Key in a `.env` File (Recommended for Secure Key Management)

To securely store and use your API keys for OpenAI, Ooba, or Tabby, create and configure a `.env` file.

**Add API Keys**:
   Add the following lines to your `.env` file. Replace `your-actual-api-key` with your actual API key for the desired service:
   ```env
   OPENAI_API_KEY=your-actual-openai-api-key
   OOBA_API_KEY=your-actual-ooba-api-key
   TABBY_API_KEY=your-actual-tabby-api-key
   ```

#### F. Set the config.ini Parameters 

1. Open the `config.ini` file located in the `Brain/` folder.

2. Locate the `[TTS]` section and update the parameters:
   ```ini
   [TTS] # Text-to-Speech configuration (about 3.4GB TTS #xttsv2 or local or TARS)
   ttsurl = http://<server-ip>:8020
   # Replace <server-ip> with the IP address of the machine running the XTTS API Server (e.g., 192.168.2.20).
   charvoice = True
   # Use character-specific voice settings.
   ttsoption = xttsv2
   # Set this to `xttsv2` to use the XTTS API Server.
   ttsclone = TARS-Short
   # Set this to the desired speaker file (e.g., `TARS-Short` or `TARS-Long`).
   ```
   - The `ttsurl` should point to the IP and port of the XTTS API Server.
   - The `ttsclone` should match the desired speaker (e.g., `TARS-Short`).

3. Locate the `[LLM]` section and update the parameters (for OpenAI):
   ```ini
   [LLM] # Large Language Model configuration (ooba/OAI or tabby)
   backend = openai
   # Set this to `openai` if using OpenAI models.
   base_url = https://api.openai.com
   # The URL for the OpenAI API.
   openai_model = gpt-4o-mini
   # Specify the OpenAI model to use (e.g., gpt-4o-mini or another supported model).
   ```
   - Confirm that the `openai_model` matches the model available with your OpenAI API key.

#### G. Run the Program
1. Navigate to the `Brain/` folder within the repository:
   ```bash
   cd Brain/
   ```
2. Start the application:
   ```bash
   python app.py
   ```
3. The program should now be running and ready to interact using your microphone and speaker.

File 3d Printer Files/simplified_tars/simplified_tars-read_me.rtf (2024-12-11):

These are fully redesigned by Michael Proctor (Manthis in Discord). I plan to slowly redesign the entire bot so future edits are easier to make (Editing STEP files can be a pain…).

Everything will be in a public Onshape project so feel free to make a copy of it and make your own edits.
I am a noob at design, so feel free to DM me on Discord any feedback you have.

Onshape Project: https://cad.onshape.com/documents/3fc66bce504b7e19d90aa795/w/4c55da55e44503ca82605304/e/a162dff2fca3f073a37a6638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

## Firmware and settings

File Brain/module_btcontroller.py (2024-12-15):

import evdev
import time
from datetime import datetime
import module_servoctl as module_servoctl
from evdev import InputDevice, categorize, ecodes, list_devices
import Adafruit_PCA9685

pwm = Adafruit_PCA9685.PCA9685(busnum=1)  # Specify I2C bus 1

#port
pwm.set_pwm(3, 3, 610)
pwm.set_pwm(4, 4, 570)
pwm.set_pwm(5, 5, 570)
#starboard
pwm.set_pwm(6, 6, 200)
pwm.set_pwm(7, 7, 200)
pwm.set_pwm(8, 8, 240)

# Set frequency to 60hz, good for servos.
pwm.set_pwm_freq(60)

lTrg = 37
rTrg = 50
upBtn = 46
downBtn = 32
lBtn = 18
rBtn = 33
xBtn = 23
yBtn = 35
aBtn = 36
bBtn = 34
minusBtn = 49
plusBtn = 24

global gamepad_path
toggle = True
pose = False

SECRET_CODE = [
    "up", "up", "down", "down", "left", "right", "left", "right", "B", "A Button", "Start Button"
]

# Track user input
input_sequence = []

def find_controller(controller_name):
    global gamepad_path
    """
    Search for a controller by its name.
    """
    devices = [InputDevice(path) for path in list_devices()]
    for device in devices:
        if controller_name.lower() in device.name.lower():
            print(f"[{datetime.now().strftime('%Y-%m-%d %H:%M:%S')}] LOAD: Controller found: {device.name} at {device.path}")
            gamepad_path = device.path
            return device
    print(f"No controller found with name: {controller_name}")
    return None

def check_secret_code(button_name):
    global input_sequence
    input_sequence.append(button_name)

    # Check if the current sequence matches the start of the secret code
    if input_sequence == SECRET_CODE[:len(input_sequence)]:
        # If the sequence matches the full secret code
        if len(input_sequence) == len(SECRET_CODE):
            from module_secrets import play_video_fullscreen
            play_video_fullscreen("media/secret.mp4", rotation_angle=90)
            input_sequence = []  # Reset the sequence after the code is entered
    else:
        # If the sequence doesn't match, reset it
        #print(f"Invalid sequence detected: {input_sequence}. Resetting...")
        input_sequence = []

#functions to move
def stepForward():
	module_servoctl.height_neutral_to_up()
	module_servoctl.torso_neutral_to_forwards()
	module_servoctl.torso_bump()
	module_servoctl.torso_return()

def turnRight():
	module_servoctl.neutral_to_down()
	module_servoctl.turn_right()
	module_servoctl.down_to_neutral()
	module_servoctl.neutral_from_right()

def turnLeft():
	module_servoctl.neutral_to_down()
	module_servoctl.turn_left()
	module_servoctl.down_to_neutral()
	module_servoctl.neutral_from_left()

def pose():
    module_servoctl.neutral_to_down()
    module_servoctl.torso_neutral_to_backwards()
    module_servoctl.down_to_up()

def unpose():
    module_servoctl.torso_return2()  
        
        
# D-Pad Actions (pressed and released)
def action_dpad_up_pressed():
    #print(f"[{datetime.now().strftime('%Y-%m-%d %H:%M:%S')}] CTRL: D-Pad Up pressed! Let's move up!")
    stepForward()

def action_dpad_down_pressed():
    #print(f"[{datetime.now().strftime('%Y-%m-%d %H:%M:%S')}] CTRL: D-Pad Down pressed! Let's move down!")
    global pose
    if pose == False:
        pose()
        pose = True
    elif pose == True:
        unpose()
        pose = False

def action_dpad_left_pressed():
    #print(f"[{datetime.now().strftime('%Y-%m-%d %H:%M:%S')}] CTRL: D-Pad Left pressed! Moving left!")
    turnLeft()

def action_dpad_right_pressed():
    #print(f"[{datetime.now().strftime('%Y-%m-%d %H:%M:%S')}] CTRL: D-Pad Right pressed! Moving right!")
    turnRight()

def action_dpad_up_released():
    #print(f"[{datetime.now().strftime('%Y-%m-%d %H:%M:%S')}] CTRL: D-Pad Up released! Stopping move up.")
    pass

def action_dpad_down_released():
    #print(f"[{datetime.now().strftime('%Y-%m-%d %H:%M:%S')}] CTRL: D-Pad Down released! Stopping move down.")
    pass

def action_dpad_left_released():
    #print(f"[{datetime.now().strftime('%Y-%m-%d %H:%M:%S')}] CTRL: D-Pad Left released! Stopping move left.")
    pass

def action_dpad_right_released():
    #print(f"[{datetime.now().strftime('%Y-%m-%d %H:%M:%S')}] CTRL: D-Pad Right released! Stopping move right.")
    pass

# Joystick Actions (show values when moved)
def action_left_stick_move(x_value, y_value):
    #print(f"[{datetime.now().strftime('%Y-%m-%d %H:%M:%S')}] CTRL: Left Stick moved to X: {x_value}, Y: {y_value}")
    pass

def action_right_stick_move(x_value, y_value):
    #print(f"[{datetime.now().strftime('%Y-%m-%d %H:%M:%S')}] CTRL: Right Stick moved to X: {x_value}, Y: {y_value}")
    pass

# Define custom actions for specific buttons (pressed)
def action_a_button_pressed():
    #print(f"[{datetime.now().strftime('%Y-%m-%d %H:%M:%S')}] CTRL: A Button? Are you trying to jump?")
    global toggle
    if toggle == True:
        module_servoctl.starHandPlus()
    elif toggle == False:
        module_servoctl.starHandMinus()

def action_b_button_pressed():
    #print(f"[{datetime.now().strftime('%Y-%m-%d %H:%M:%S')}] CTRL: Oh no, the B! Self-destruct initiated... just kidding!")
    global toggle
    if toggle == True:
        module_servoctl.portHandPlus()
    elif toggle == False:
        module_servoctl.portHandMinus()

def action_x_button_pressed():
    #print(f"[{datetime.now().strftime('%Y-%m-%d %H:%M:%S')}] CTRL: Hey, stop pushing my X Button!")
    global toggle
    if toggle == True:
        module_servoctl.starForarmPlus()
    elif toggle == False:
        module_servoctl.starForarmMinus()

def action_y_button_pressed():
    #print(f"[{datetime.now().strftime('%Y-%m-%d %H:%M:%S')}] CTRL: Y Button? I hope you know what youre doing!")
    global toggle
    if toggle == True:
        module_servoctl.portForarmPlus()
    elif toggle == False:
        module_servoctl.portForarmMinus()

def action_r1_button_pressed():
    #print(f"[{datetime.now().strftime('%Y-%m-%d %H:%M:%S')}] CTRL: R1 Button pressed! Thats the turbo button!")
    global toggle
    if toggle == True:
        module_servoctl.starMainPlus()
    elif toggle == False:
        module_servoctl.starMainMinus()

def action_l1_button_pressed():
    #print(f"[{datetime.now().strftime('%Y-%m-%d %H:%M:%S')}] CTRL: L1 Button activated! Shields up!")
    global toggle
    if toggle == True:
        module_servoctl.portMainPlus()
    elif toggle == False:
        module_servoctl.portMainMinus()

def action_r2_button_pressed():
    #print(f"[{datetime.now().strftime('%Y-%m-%d %H:%M:%S')}] CTRL: R2 Button? Are we accelerating now?")
    pass

def action_l2_button_pressed():
    #print(f"[{datetime.now().strftime('%Y-%m-%d %H:%M:%S')}] CTRL: L2 Button pressed! Steady... dont crash!")
    pass

def action_bottom_button_pressed():
    #print(f"[{datetime.now().strftime('%Y-%m-%d %H:%M:%S')}] CTRL: Bottom Button? What kind of mischief is this?")
    pass

def action_select_button_pressed():
    #print(f"[{datetime.now().strftime('%Y-%m-%d %H:%M:%S')}] CTRL: Select Button pressed. Are you opening a menu?")
    pass

def action_start_button_pressed():
    #print(f"[{datetime.now().strftime('%Y-%m-%d %H:%M:%S')}] CTRL: Start Button pressed. Game on!")
    pass

def LJoyStick_button_pressed():
    #print(f"[{datetime.now().strftime('%Y-%m-%d %H:%M:%S')}] CTRL: L JoyStick Pressed. HAHAHAHAHA")
    pass

def RJoyStick_button_pressed():
    #print(f"[{datetime.now().strftime('%Y-%m-%d %H:%M:%S')}] CTRL: R JoyStick Pressed. Be Careful!")
    pass

# Define custom actions for specific buttons (released)
def action_a_button_released():
    #print(f"[{datetime.now().strftime('%Y-%m-%d %H:%M:%S')}] CTRL: Okay, you stopped jumping. Good!")
    pass

def action_b_button_released():
    #print(f"[{datetime.now().strftime('%Y-%m-%d %H:%M:%S')}] CTRL: B released. Crisis averted!")
    pass

def action_x_button_released():
    #print(f"[{datetime.now().strftime('%Y-%m-%d %H:%M:%S')}] CTRL: Thats better. Leave my X Button alone!")
    pass

def action_y_button_released():
    #print(f"[{datetime.now().strftime('%Y-%m-%d %H:%M:%S')}] CTRL: Y Button released. Thank you for being cautious!")
    pass

def action_r1_button_released():
    #print(f"[{datetime.now().strftime('%Y-%m-%d %H:%M:%S')}] CTRL: Turbo disengaged. R1 Button safe!")
    pass

def action_l1_button_released():
    #print(f"[{datetime.now().strftime('%Y-%m-%d %H:%M:%S')}] CTRL: Shields down. L1 Button released!")
    pass

def action_r2_button_released():
    #print(f"[{datetime.now().strftime('%Y-%m-%d %H:%M:%S')}] CTRL: R2 Button released. No more speeding!")
    global toggle
    print("+")
    toggle = True

def action_l2_button_released():
    #print(f"[{datetime.now().strftime('%Y-%m-%d %H:%M:%S')}] CTRL: L2 Button released. Smooth landing!")
    global toggle
    print("-")
    toggle = False

def action_bottom_button_released():
    #print(f"[{datetime.now().strftime('%Y-%m-%d %H:%M:%S')}] CTRL: Bottom Button released. Mischief managed!")
    pass

def action_select_button_released():
    #print(f"[{datetime.now().strftime('%Y-%m-%d %H:%M:%S')}] CTRL: Select Button released. Menu closed!")
    pass

def action_start_button_released():
    #print(f"[{datetime.now().strftime('%Y-%m-%d %H:%M:%S')}] CTRL: Start Button released. Lets pause for a moment.")
    pass

def LJoyStick_button_released():
    #print(f"[{datetime.now().strftime('%Y-%m-%d %H:%M:%S')}] CTRL: L JoyStick released. That tickled.")
    pass

def RJoyStick_button_released():
    #print(f"[{datetime.now().strftime('%Y-%m-%d %H:%M:%S')}] CTRL: R JoyStick released. Whew!.")
    pass

def start_controls():
    """
    Listen to gamepad events and execute actions based on button presses/releases and analog movements.
    """
    # Retry loop for detecting the gamepad
    gamepad = None
    while gamepad is None:
        try:
            # Try to connect to the gamepad
            gamepad = evdev.InputDevice(gamepad_path)
            print(f"[{datetime.now().strftime('%Y-%m-%d %H:%M:%S')}] LOAD: {gamepad.name} connected.")
        except FileNotFoundError:
            time.sleep(5)  # Wait before retrying

    # Define mappings for button events with actions
    button_map = {
        evdev.ecodes.BTN_SOUTH: ("A Button", action_a_button_pressed, action_a_button_released),
        evdev.ecodes.BTN_EAST: ("B", action_b_button_pressed, action_b_button_released),
        evdev.ecodes.BTN_NORTH: ("X Button", action_x_button_pressed, action_x_button_released),
        evdev.ecodes.BTN_WEST: ("Y Button", action_y_button_pressed, action_y_button_released),
        311: ("R1 Button", action_r1_button_pressed, action_r1_button_released),
        310: ("L1 Button", action_l1_button_pressed, action_l1_button_released),
        313: ("R2 Button", action_r2_button_pressed, action_r2_button_released),
        312: ("L2 Button", action_l2_button_pressed, action_l2_button_released),
        306: ("Bottom Button", action_bottom_button_pressed, action_bottom_button_released),
        314: ("Select Button", action_select_button_pressed, action_select_button_released),
        315: ("Start Button", action_start_button_pressed, action_start_button_released),
        317: ("L JoyStick", LJoyStick_button_pressed, LJoyStick_button_released),
        318: ("R JoyStick", RJoyStick_button_pressed, RJoyStick_button_released),
    }

    # Define mappings for analog events
    analog_map = {
        evdev.ecodes.ABS_HAT0Y: {"up": action_dpad_up_pressed, "down": action_dpad_down_pressed},
        evdev.ecodes.ABS_HAT0X: {"left": action_dpad_left_pressed, "right": action_dpad_right_pressed},
        evdev.ecodes.ABS_X: "Left Stick X",
        evdev.ecodes.ABS_Y: "Left Stick Y",
        evdev.ecodes.ABS_Z: "Right Stick X",
        evdev.ecodes.ABS_RZ: "Right Stick Y",
        9: "Trigger Axis",  # Example label for Unknown Axis 9
    }

    print(f"[{datetime.now().strftime('%Y-%m-%d %H:%M:%S')}] LOAD: Controls Listening...")
    try:
        dpad_state = {"up": False, "down": False, "left": False, "right": False}
        
        for event in gamepad.read_loop():
            if event.type == evdev.ecodes.EV_KEY:  # Button press/release
                button_info = button_map.get(event.code)
                if button_info:
                    button_name, button_action_pressed, button_action_released = button_info
                    if event.value == 1:  # Button pressed
                        button_action_pressed()  # Call the associated pressed action
                        check_secret_code(button_name)
                    elif event.value == 0:  # Button released
                        button_action_released()  # Call the associated released action
                else:
                    print(f"[{datetime.now().strftime('%Y-%m-%d %H:%M:%S')}] MOVE: Unknown Button {event.code}")
            elif event.type == evdev.ecodes.EV_ABS:  # Analog stick or D-pad movement
                #print(f"[{datetime.now().strftime('%Y-%m-%d %H:%M:%S')}] MOVE: Event Code: {event.code}, Event Value: {event.value}")

                if event.code == evdev.ecodes.ABS_HAT0Y:
                    if event.value < 0 and not dpad_state["up"]:  # Up pressed
                        action_dpad_up_pressed()
                        check_secret_code("up")
                        dpad_state["up"] = True
                        dpad_state["down"] = False
                    elif event.value > 0 and not dpad_state["down"]:  # Down pressed
                        action_dpad_down_pressed()
                        check_secret_code("down")
                        dpad_state["down"] = True
                        dpad_state["up"] = False
                    elif event.value == 0:  # Released
                        if dpad_state["up"]:
                            action_dpad_up_released()
                        if dpad_state["down"]:
                            action_dpad_down_released()
                        dpad_state["up"] = False
                        dpad_state["down"] = False


                # Handle Left and Right (ABS_HAT0X)
                elif event.code == evdev.ecodes.ABS_HAT0X:
                    if event.value < 0 and not dpad_state["left"]:  # Left pressed
                        action_dpad_left_pressed()
                        check_secret_code("left")
                        dpad_state["left"] = True
                        dpad_state["right"] = False
                    elif event.value > 0 and not dpad_state["right"]:  # Right pressed
                        action_dpad_right_pressed()
                        check_secret_code("right")
                        dpad_state["right"] = True
                        dpad_state["left"] = False
                    elif event.value == 0:  # Released
                        if dpad_state["left"]:
                            action_dpad_left_released()
                        if dpad_state["right"]:
                            action_dpad_right_released()
                        dpad_state["left"] = False
                        dpad_state["right"] = False



                elif event.code == evdev.ecodes.ABS_X:  # Left Stick X Axis
                    action_left_stick_move(event.value, 0)  # Y value isn't used here
                elif event.code == evdev.ecodes.ABS_Y:  # Left Stick Y Axis
                    action_left_stick_move(0, event.value)  # X value isn't used here
                elif event.code == evdev.ecodes.ABS_Z:  # Right Stick X Axis
                    action_right_stick_move(event.value, 0)  # Y value isn't used here
                elif event.code == evdev.ecodes.ABS_RZ:  # Right Stick Y Axis
                    action_right_stick_move(0, event.value)  # X value isn't used here

    except KeyboardInterrupt:
        print("\nExiting...")

    # Clean up
    gamepad.close()

    # Clean up
    gamepad.close()

controller_name = "8BitDo"  # Replace with part of your controller's name
device = find_controller(controller_name)

#Delete this is for testing
if __name__ == "__main__":
    while True:
        try:
            start_controls()
        except Exception as e:
            print(f"An error occurred: {e}")
            # Optionally add a small delay to prevent tight infinite loops in case of failure
            import time
            time.sleep(1)

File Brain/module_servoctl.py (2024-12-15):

from __future__ import division
import time
import Adafruit_PCA9685
from threading import Thread

pwm = Adafruit_PCA9685.PCA9685(busnum=1)  # Specify I2C bus 1

# Set frequency to 60hz, good for servos.
pwm.set_pwm_freq(60)

portMain = 610
starMain = 200
portForarm = 570
starForarm = 200
portHand = 570
starHand = 240

# Center Lift Servo (0) Values
upHeight = 205
neutralHeight = 275
downHeight = 450

# Port Drive Servo (1) Values
forwardPort = 440
neutralPort = 375
backPort = 330

# Starboard Drive Servo (2) Values
forwardStarboard = 292
neutralStarboard = 357
backStarboard = 402

# moves the torso from a neutral position upwards, allowing the torso to pivot forwards or backwards
def height_neutral_to_up():
	height = neutralHeight
	print('setting center servo (0) Neutral --> Up position')
	while (height > upHeight):
		height = height - 1
		pwm.set_pwm(0, 0, height)
		time.sleep(0.001)
	print('center servo (0) set to: Up position\n ')

# rotates the torso outwards, enough so that when TARS pivots and lands, the bottom of the torso is 
# flush with the ground. Making the torso flush with the ground is an intentional improvement from
# previous programs, where TARS would land and then slide a little on smooth surfaces, which while
# allowing for a simple walking program, inhibited TARS' ability to walk on surfaces with different 
# coefficients of friction
def torso_neutral_to_forwards():
	port = neutralPort
	starboard = neutralStarboard
	print('setting port and starboard servos (1)(2) Neutral --> Forward')
	while (port < forwardPort):
		port = port + 1
		starboard = starboard - 1
		pwm.set_pwm(1, 1, port)
		pwm.set_pwm(2, 2, starboard)
		time.sleep(0.0001)
	print('port and starboard servos (1)(2) set to: Forward position\n ')

def torso_neutral_to_backwards():
	port = neutralPort
	starboard = neutralStarboard
	print('setting port and starboard servos (1)(2) Neutral --> Forward')
	while (port > backPort):
		port = port - 1
		starboard = starboard + 1
		pwm.set_pwm(1, 1, port)
		pwm.set_pwm(2, 2, starboard)
		time.sleep(0.0001)
	print('port and starboard servos (1)(2) set to: Forward position\n ')

# rapidly shifts the torso height from UP --> DOWN and then returns --> UP, which should cause TARS 
# to pivot and land on it's torso
def torso_bump():
	height = upHeight
	print('performing a torso bump\nsetting center servo (0) Up --> Down position FAST')
	while (height < downHeight):
		height = height + 2
		pwm.set_pwm(0, 0, height)
		time.sleep(0.000001)
	print('setting center servo (0) Down --> Up position FAST')
	while (height > upHeight):
		height = height - 1
		pwm.set_pwm(0, 0, height)
		time.sleep(0.0001)
	print('center servo (0) returned to Up position\n')
	
# returns the torso's vertical height and rotation to centered values from up height and forward 
# rotation. Activates two external functions so movement in both axes can occur in parallel.
def torso_return():
	t1 = Thread(target = torso_return_rotation)
	t2 = Thread(target = torso_return_vertical)
	
	t1.start()
	t2.start()

# returns torso's rotation to neutral from forward
def torso_return_rotation():
	port = forwardPort
	starboard = forwardStarboard
	print('setting port and starboard servos (1)(2) Forward --> Neutral position')
	while (port > neutralPort):
		port = port - 1
		starboard = starboard + 1
		pwm.set_pwm(1, 1, port)
		pwm.set_pwm(2, 2, starboard)
		time.sleep(0.005)
	print('port and starboard servos (1)(2) set to: Neutral position\n ')

# returns torso's vertical to neutral from up	
def torso_return_vertical():
	height = upHeight
	print('setting center servo (0) Up --> Down position')
	# moving the torso down to create clearance for the rotation of the legs
	while (height < downHeight):
		height = height + 1
		pwm.set_pwm(0, 0, height)
		time.sleep(0.00005)
	# moving the torso up from down to neutral
	#time.sleep(.2)
	while (height > neutralHeight):
		height = height - 1
		pwm.set_pwm(0, 0, height)
		time.sleep(0.00001)
	print('center servo (0) set to: Neutral position\n ')

def torso_return2():
	t1 = Thread(target = torso_return_rotation2)
	t2 = Thread(target = torso_return_vertical2)
	
	t1.start()
	t2.start()

# returns torso's rotation to neutral from forward
def torso_return_rotation2():
	port = backPort
	starboard = backStarboard
	print('setting port and starboard servos (1)(2) Forward --> Neutral position')
	while (port < neutralPort):
		port = port + 1
		starboard = starboard - 1
		pwm.set_pwm(1, 1, port)
		pwm.set_pwm(2, 2, starboard)
		time.sleep(0.01)
	print('port and starboard servos (1)(2) set to: Neutral position\n ')

# returns torso's vertical to neutral from up	
def torso_return_vertical2():
	height = upHeight
	print('setting center servo (0) Up --> Down position')
	# moving the torso down to create clearance for the rotation of the legs
	while (height < downHeight):
		height = height + 1
		pwm.set_pwm(0, 0, height)
		time.sleep(0.001)
	# moving the torso up from down to neutral
	time.sleep(.25)
	while (height > neutralHeight):
		height = height - 1
		pwm.set_pwm(0, 0, height)
		time.sleep(0.001)
	print('center servo (0) set to: Neutral position\n ')


# moves the torso from neutral position to down
def neutral_to_down():
    height = neutralHeight
    print('setting center servo (0) Neutral --> Down position')
    while (height < downHeight):
        height = height + 1
        pwm.set_pwm(0, 0, height)
        time.sleep(0.001)
        
def down_to_up():
    height = downHeight
    print('setting center servo (0) Down --> Neutral position')
    while (height > upHeight):
        height = height - 1
        pwm.set_pwm(0, 0, height)
        time.sleep(0.001)

def down_to_neutral():
    height = downHeight
    print('setting center servo (0) Down --> Neutral position')
    while (height > neutralHeight):
        height = height - 1
        pwm.set_pwm(0, 0, height)
        time.sleep(0.001)

def neutral_to_down():
    height = neutralHeight
    print('setting center servo (0) Down --> Neutral position')
    while (height < downHeight):
        height = height + 1
        pwm.set_pwm(0, 0, height)
        time.sleep(0.001)


def turn_right():
    port = neutralPort
    starboard = neutralStarboard
    while (port < forwardPort):
        port = port + 1
        starboard = starboard + 1
        pwm.set_pwm(1, 1, port)
        pwm.set_pwm(2, 2, starboard)
        time.sleep(0.001)
        
def turn_left():
    port = neutralPort
    starboard = neutralStarboard
    while (port > backPort):
        port = port - 1
        starboard = starboard - 1
        pwm.set_pwm(1, 1, port)
        pwm.set_pwm(2, 2, starboard)
        time.sleep(0.001)
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

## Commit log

2024-11-19 new file: 3d Printer Files/525132 v1 (1).stl new file: 3d Printer Files/535132 v1.stl new file: 3d Printer Files/Axle.stl new file: 3d Printer Files/Bearing (1).stl new file: 3d Printer Files/Chassis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
    [525125.STEP, 525132 v1 (1).stl, 535132 v1.stl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]
2024-11-23 modified: 3d Printer Files/GPTARs Files.3mf new file: CharacterCard/TARS alpha.json new file: CharacterCard/TARS beta.json new file: CharacterCard/TARS charlie.json new file: CharacterCard/TARS delta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
    [GPTARs Files.3mf]
2024-11-23 new file: 3d Printer Files/Alternate Lid Lower.stl new file: 3d Printer Files/Alternate Lid.stl new file: 3d Printer Files/Chassis (Bottom).stl new file: 3d Printer Files/Chassis Bottom (Mod SD CARD)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
    [Alternate Lid Lower.stl, Alternate Lid.stl, Chassis (Bottom).stl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]
2024-11-24 deleted: 3d Printer Files/Chassis (Bottom).stl renamed: 3d Printer Files/Chassis (2).stl -> 3d Printer Files/Chassis (Orginal).stl modified: 3d Printer Files/GPTARs Files.3mf new file: 3d Printer Fil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
    [Chassis (Bottom).stl, Chassis (Orginal).stl, GPTARs Files.3mf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]
2024-11-26 new file: PrintComplete.jpg modified: README.md
2024-11-28 modified: 3d Printer Files/525132 v1 (1).stl modified: 3d Printer Files/535132 v1.stl modified: 3d Printer Files/Alternate Lid Lower.stl modified: 3d Printer Files/Alternate Lid.stl modified: 3d Prin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
    [3.5 LCD LID TOP Letters.stl, 3.5 LCD LID TOP.stl, 3.5 Lid Top combined.stl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]
2024-11-28 Upload of inital brain, very much a WIP. dont ask.
    [training_data.csv]
2024-11-30 new file: 3d Printer Files/TARS 3 v9Lower Chasis.stl new file: 3d Printer Files/TARS 3 v9Lower Lid.stl new file: 3d Printer Files/TARS Bottom Mod V9 chasis.stl
    [TARS 3 v9Lower Chasis.stl, TARS 3 v9Lower Lid.stl, TARS Bottom Mod V9 chasis.stl]
2024-11-30 renamed: 3d Printer Files/GPTARs Files.3mf -> 3d Printer Files/3MF File/GPTARs Files.3mf deleted: 3d Printer Files/525132 v1 (1).stl renamed: 3d Printer Files/Port Lid A.stl -> 3d Printer Files/Arm C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
    [3.5 LCD LID TOP Letters.stl, 3.5 LCD LID TOP.stl, 3.5 Lid Top combined.stl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]
2024-11-30 new file: 3d Printer Files/Chassis Connector CAMERA Support.stl new file: 3d Printer Files/Chassis Lower (v9) SDCARD and DIY Servo MOD.stl new file: 3d Printer Files/Chassis Lower Servo Mount (DIY Se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
    [Chassis Connector CAMERA Support.stl, Chassis Lower (v9) SDCARD and DIY Servo MOD.stl, Chassis Lower Servo Mount (DIY Servo).stl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]
2024-12-01 Screw position move
    [TARS_ScreenLid.stl]
2024-12-01 Chassis Upper Lid (v9) Modded Holes
    [Chassis Upper Lid (v9) Modded Holes.stl]
2024-12-01 new file: 3d Printer Files/Other/RPI_Fan_Mount.stl new file: 3d Printer Files/Other/RPI_Fan_Mount_Credit.txt
    [RPI_Fan_Mount.stl]
2024-12-03 slimmed sus mounts -1mm for low friction movement. increase infill if desired
    [susmount_x2_MOD90pctWide(v9).stl]
2024-12-03 smaller servo bracket for different servo wiring locations
    [UpperChassis_MODshortServoBracket(v9).stl]
2024-12-04 renamed to match related part naming convention
    [ChassisUpper_MODshortServoBracket(v9).stl]
2024-12-05 ENVSETUP - Raspberry Pi GPTARS Env Setup instructions
2024-12-05 trimmed battery clip to allow more battery size/position/type variations. use electrical tape to fasten.
    [Chassis Lower Lid MOD open batt clip(v10).stl]
2024-12-06 v9 open battery clip for more battery size/pos options. use electrical tape to secure.
    [Chassis Lower Lid MOD open batt clip (v9).stl]
2024-12-06 Fix configuration param extraction bug
    [module_main.py]
2024-12-07 added slots for velco strap use. added 1.5mm between the tabs to allow room for strap clearance.
    [Chassis Lower Lid MOD slotted open batt bracket (v10).stl]
2024-12-09 Redesigned the legs of Tars by removing the fingers and simplifying them for printing
    [footpad-simplified.3mf, footpad-simplified.step, leg - simplified.3mf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]
2024-12-09 simpliified tars legs
    [footpad-simplified.3mf, footpad-simplified.step, leg - simplified.3mf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]
2024-12-13 new file: 3d Printer Files/Other/pct credit.txt
2024-12-14 Made some mods
    [Arm Left Lower Chassis MOD 3mm servoscrews.stl, Arm Right Lower Chassis MOD 3mm servoscrews.stl, Arm Right&Left Mount Bigger bearinghole.stl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]
